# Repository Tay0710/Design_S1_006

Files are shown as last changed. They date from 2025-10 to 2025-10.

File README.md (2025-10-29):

# ELEC5550 Group Project (Team 0-06)

**Students Involved:**
- Aidan	Wheller
- Dorothy	Jong
- Emersyn Johnson
- Owen Spicer
- Samuel Dixon
- Taylah Karran

## 🚀 Project Summary

This project integrates hardware, firmware, and design elements to develop a fully functional autonomous 3D mapping drone system. This iteration of the design involves a drone capable of autonomously navigating the operation environment of Lv4 EECE, a LoRa-based kill switch which covers the entire operation environment, a mapping test rig used to manually collect data from 2 independent mapping systems, and a 3D mapping python pipeline which runs on the base station, used to convert raw mapping data from the test rig into 2 independent maps plus a combined map.

The next iteration of this design aims to combine the mapping test rig with the autonomous drone platform, creating a fully integrated autonomous 3D mapping drone system which follows the system architecture diagram below.

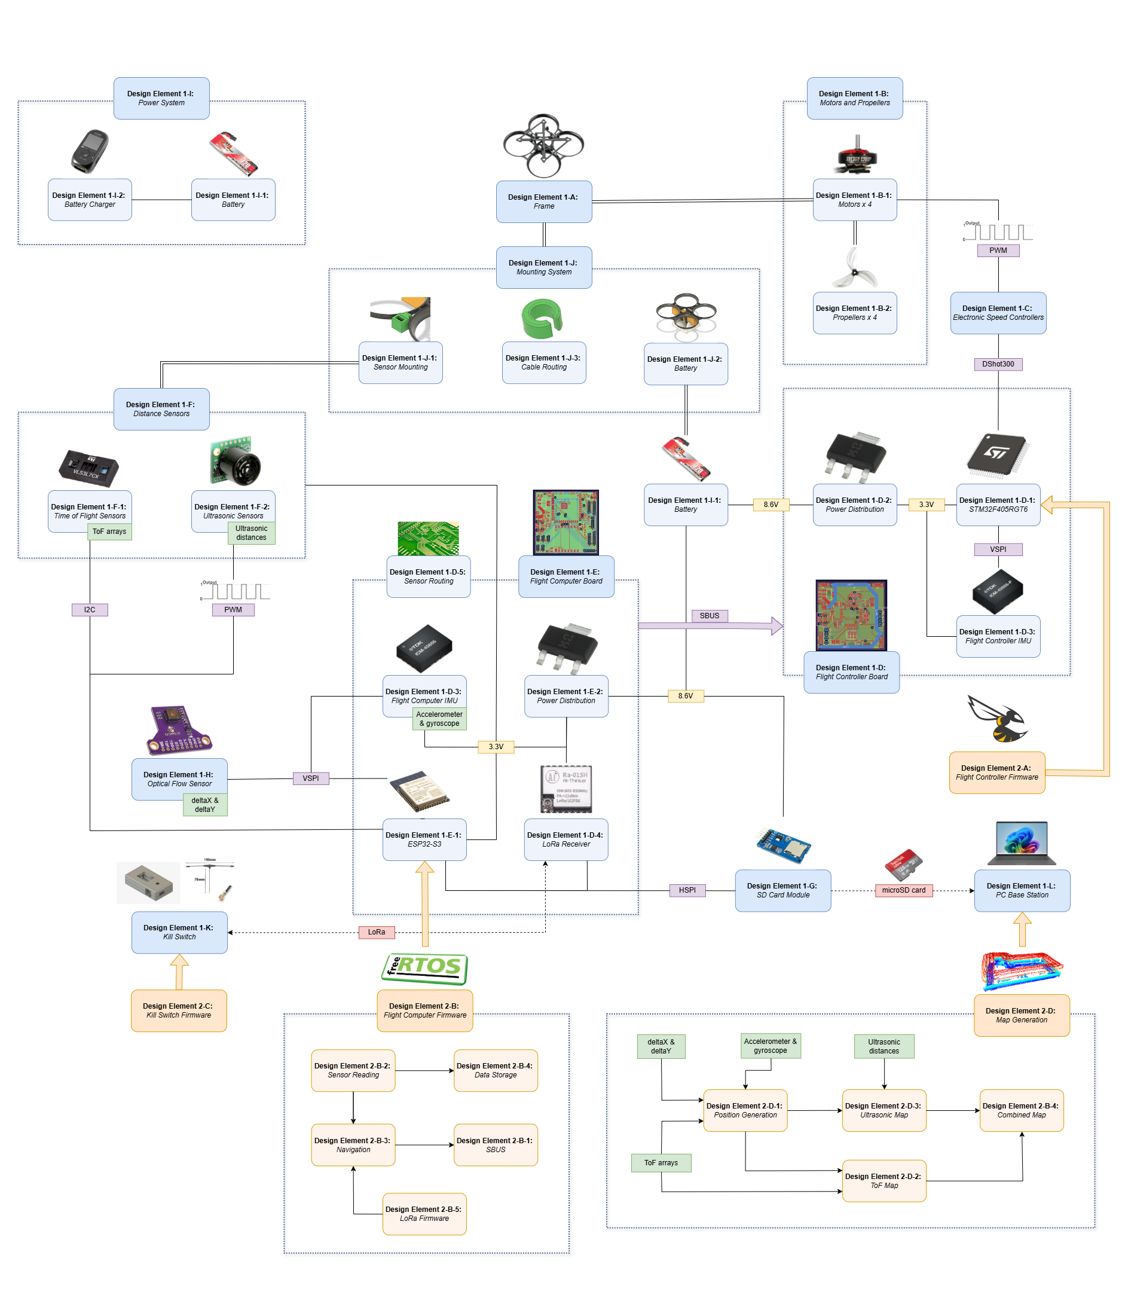
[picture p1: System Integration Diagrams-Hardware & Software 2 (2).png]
System Architecture


## 📁 Folder Structure

```
📁 Root Directory

├── 📂 3D Mapping
│   └── 3D mapping
│   └── optical_flow_method
│   └── optical_flow_method_data
│
├── 📂 CAD Design
│   └── 3D-printed Parts
│   └── Full_Model
│   └── LoRa Kill Switch
│
├── 📂 Drone Firmware
│   └── Flight Computer Firmware
│   └── Flight Controller Firmware
│
├── 📂 LoRa Drone Receiver Test Firmware
│   └── LORA_DRONE_RECEIVER
│
├── 📂 LoRa Kill Switch Firmware
│   └── LORA_TRANSMITTER_BUTTON
│
├── 📂 PCB Design
│   └── ESP32_BOARD_V2
│   └── STM32_BOARD_V3
│
├── 📂 Test Rig Firmware
│   └── Test Rig Data Collection
│   └── Test Rig FreeRTOS
│
└── 📂 Videos
```

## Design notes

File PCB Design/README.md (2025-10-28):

# ELEC5550 Group Project (Team 0-06)

**Students Involved:**
- Aidan	Wheller
- Dorothy Jong
- Emersyn Johnson
- Owen Spicer
- Samuel Dixon
- Taylah Karran

## 📁 Project Overview - PCB Design

**Folder Summary:**

This folder contains all PCB schematics, design files, and related documentation required for manufacturing the printed circuit board (PCB) for the ESP32 flight computer and STM32 flight controller. It includes the necessary Gerber files, bill of materials (BOM), and design source files to ensure accurate production and assembly. All PCB projects can be viewed through KiCAD, which can be downloaded through this [link](https://www.kicad.org/download/).

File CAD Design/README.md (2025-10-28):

# ELEC5550 Group Project (Team 0-06)

**Students Involved:**
- Aidan	Wheller
- Dorothy Jong
- Emersyn Johnson
- Owen Spicer
- Samuel Dixon
- Taylah Karran

## 📁 Project Overview - CAD Design

**Folder Summary:**

This folder contains all the CAD and STL files required to replicate the design. The CAD files can be used for editing in your preferred CAD software, and the STL files are ready for 3D printing. More specifically, it contains:
- LoRa Kill Switch: CAD and STL files for the LoRa Kill Switch Case.
- Full_Model: CAD project (on Fusion) for the drone assembly, including the drone frame, launch pad, launch rail and sensors mounts.
- 3D-printed Parts: STL files for the launch pad, launch rail, and various sensors mounts which were 3D-printed.

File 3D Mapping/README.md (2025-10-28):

# ELEC5550 Group Project

**Students Involved:**
- Aidan	Wheller
- Dorothy Jong
- Emersyn Johnson
- Owen Spicer
- Samuel Dixon
- Taylah Karran

## 📁 Project Overview
This repository contains all scripts used to process sensor data and generate a **3D map** of an indoor environment using a drone platform equipped with:
- PMW3901 Optical Flow Sensor  
- VL53L7CX Time-of-Flight (ToF) Sensor  
- Ultrasonic Distance Sensors (U, D, L, R)  
- ICM-45686 IMU  

The system estimates **drone position and orientation** in the world frame and then maps the environment using synchronized ToF and Ultrasonic readings.

---

## Execution Order

### **A. Install the Virtual Environment**
1. From the project root folder, run:
        python -m venv venv
2. Run the virtual environment:
        .\venv\Scripts\activate
3. Install all required packages:
        pip install -r requirements.txt
Note: to get open3d working must use python 11 or below.

### **B. Position and Trajectory Estimation**
1. Open the optical flow position folder:
        cd optical_flow_method
2. Update the filepath in x0_position_pipeline.py
3. Run the position pipeline:
        python x0_position_pipeline.py

### **C. Point Cloud Generation**
1. Exit the optical flow folder:
        cd ..
2. Open the 3D mapping folder:
        cd 3D mapping
3. Update the filepath in x0_mapping_pipeline_V3.py
4. Run the mapping pipeline:
        python x0_mapping_pipeline_V3.py
##

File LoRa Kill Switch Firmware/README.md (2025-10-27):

# ELEC5550 Group Project (Team 0-06)

**Students Involved:**
- Aidan	Wheller
- Dorothy Jong
- Emersyn Johnson
- Owen Spicer
- Samuel Dixon
- Taylah Karran

## 📁 Project Overview - LoRa Kill Switch Firmware

This folder contains the firmware for the LoRa Kill Switch. It is intended for a LilyGo T3 S3 SX1262 board with an IPEX-connected 915 MHz T-antenna. This firmware is responsible for sending LoRa messages periodically to the LoRa receiver on the flight computer PCB. 

---
## Execution Order
### **A. Install VSCode and PlatformIO**
1. To run PlatformIO, download VSCode from the following [link](https://platformio.org/platformio-ide).
1. Open Extensions in VSCode and download PlatformIO from VSCode Extensions.

### **B. Uploading the Firmware**
1. Open the LORA_TRANSMITTER_BUTTON folder as a project in PlatformIO.
1. Connect the LilyGo T3 S3 SX1262 board to your PC via the USB-C port. Note: Ensure that the LilyGo T3 SX1262 board power switch is turned on.
1. Click the upload button on the PlatformIO to upload the firmware. Note: you may need to enter boot mode. To do this, open the case and press the boot button when resetting or powering on the board.

### **C. Using the LoRa Kill Switch**
1. To use the LoRa Kill Switch, power it using a USB-C cable.
1. Make sure that the T-antenna is connected properly.
1. Turn on the kill switch via the power switch at the bottom.
1. To start autonomous operation on the drone, press the red button once (as stated on the OLED display).
1. To stop the drone, press the red button a second time.

Note: make sure that the kill switch is not transmitting any LoRa messages when the drone is first powered on.

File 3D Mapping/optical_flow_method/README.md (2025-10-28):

This is the code for the 3D drone trajectory.
To update this for new samples:
    - Run x0_position_pipeline.py to update all position data.

To run:
    - Run x0_mapping_pipeline.py to generate the drone trajectory in world frame.

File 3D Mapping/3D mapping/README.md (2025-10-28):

This is the code for the 3D mapping using the position calculated in the pipeline.
To update this for new samples:
    - Run x0_mapping_pipeline_V3.py to update all position data.

To run:
    - Run x0_mapping_pipeline_V3.py to generate point clouds of the:
        1. ToFs
        2. Ultrasonics
        3. Fused Map

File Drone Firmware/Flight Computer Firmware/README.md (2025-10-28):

# ELEC5550 Group Project (Team 0-06)

**Students Involved:**
- Aidan	Wheller
- Dorothy Jong
- Emersyn Johnson
- Owen Spicer
- Samuel Dixon
- Taylah Karran

## 📁 Project Overview - Flight Computer Firmware

This folder contains the flight computer firmware intended for the custom flight computer PCB. The purpose of this firmware is to autonomously fly the drone by sending flight commands, through SBUS protocol, which are generated by the onboard flight control algorithms. The autonomous flight control algorithm is largely based on a left-wall following algorithm, with ultrasonic and ToF array sensors used to detect the walls and other obstacles. The drone maintains a constant distance from the wall by adjusting its roll (sent via SBUS) using a modified PD-control loop.

---
## Execution Order
### **A. Install VSCode and PlatformIO**
1. To run PlatformIO, download VSCode from the following [link](https://platformio.org/platformio-ide).
1. Open Extensions in VSCode and download PlatformIO from VSCode Extensions.

### **B. Uploading the Firmware** 
1. Open the Flight_Computer_Autonomous_Flight folder as a project in PlatformIO.
1. Connect the ESP32-S3 flight computer board to your PC via the USB micro-B port.
1. Click the upload button on the PlatformIO to upload the firmware. Note: you may need to enter boot mode. To do this, press the boot button when resetting or powering on the board.

### **C. Executing a Scan**
1. Remove USB connection to laptop/PC.
2. Make sure that the LoRa kill switch is switched off.
3. As instructed in the user manual, make sure to position the drone using the launch rails and launch pad. Plug in the 2S battery. Wait 5 seconds for the IMU to calibrate.
4. Remove the launch rails and place the drone on the launch pad at the starting position.
5. Power on the LoRa kill switch.
6. To begin autonomous operation, press the red button on the LoRa kill switch. The OLED display on the kill switch displays the message being transmitted.
7. To stop autonomous opeartion, press the red button on the LoRa kill switch again to send a "STOP" message, killing power to all the motors within 5 seconds.

Note: the red LED on the flight controller PCB indicates that the PCB is being powered.

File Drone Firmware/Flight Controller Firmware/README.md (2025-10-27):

# ELEC5550 Group Project (Team 0-06)

**Students Involved:**
- Aidan	Wheller
- Dorothy Jong
- Emersyn Johnson
- Owen Spicer
- Samuel Dixon
- Taylah Karran

## 📁 Project Overview - Flight Controller Firmware (BetaFlight)

This folder contains the flight controller firmware intended for the STM32F405RGT6 microcontroller on the flight controller PCB. The purpose of this firmware is to manage and stabilise the vehicle’s flight dynamics, processing IMU data and control inputs to generate precise motor and actuator commands.
The firmware is based on the open-source project *BetaFlight*, with a custom configuration tailored specifically for this system. 

---
## Execution Order
### **A. Install STM32CubeProgrammer**
1. Download the STM32CubeProgrammer from this [link](https://www.st.com/en/development-tools/stm32cubeprog.html).
1. Make sure to download the correct version for your PC.

### **B. Flashing the Firmware**
1. Download FLIGHT_CONTROLLER_V1.hex.
1. Open the *STM32CubeProgrammer*.
1. Using an ST-Link, connect SWDIO, SWDCLK, VDD and GND on the flight controller PCB to a PC running STM32CubeProgrammer.
1. Select 'ST-LINK' as the flashing method.
1. Go to the 'Erase & Programming' tab and select the file path of the FLIGHT_CONTROLLER_V1.hex file.
1. Click 'Start Programming' to flash the firmware onto the flight controller PCB.

Note: the LED on the flight controller PCB will start to flash, indicating that the firmware has been uploaded correctly.

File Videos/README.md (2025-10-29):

# ELEC5550 Group Project (Team 0-06)

**Students Involved:**
- Aidan	Wheller
- Dorothy Jong
- Emersyn Johnson
- Owen Spicer
- Samuel Dixon
- Taylah Karran

## 📁 Project Overview - Videos

This folder contains videos of the drone system in operation.

---
## Video Descriptions

### **Drone_Autonomous_Flight_Compressed.mp4**
This video was filmed after hours. It shows the drone successfully navigating autonomously down the length of the hallway, then turning right upon reaching a wall, and then navigating down the second hallway. No bystanders or uninvolved personnel were present during filming for safety reasons.

### **Custom_PCB_Motor_Test_Video.mp4**
This video shows each motor in operation while connected to our custom flight controller PCB and commercial ESCs.

### **Left_Turn_Video.mp4**
This video shows the drone autonomously turning left when there is a corner. This was filmed in the designated testing zone of the Lycopodium Laboratory.

### **Video_From_Demonstration**
This is the video from the official demonstration.

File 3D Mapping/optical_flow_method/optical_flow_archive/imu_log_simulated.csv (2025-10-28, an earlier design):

millis | ax | ay | az | gx | gy | gz
0 | 0.0 | 0.0 | 0.0 | 0.0 | 0.0 | 0.0
10 | 0.003970010072162657 | -0.004143366628477348 | 1.009922869792396 | 0.04246248867841663 | -0.023719845371533477 | 0.03823164368084453
20 | -0.005630144648727487 | 0.006787736788023693 | 1.003133558558664 | 0.06204213521290253 | -0.03606169442252252 | 0.044796276796084264
30 | -0.005310671083645506 | -0.01964439691232883 | 1.0145801393593221 | 0.05388330169073391 | -0.021868536522935647 | 0.0386054729523965
40 | 0.006911457807997143 | 0.0003999330672221197 | 1.0043240633648682 | 0.06436539555835025 | -0.033661465325746945 | 0.03786024592444924
50 | -0.00151988489667531 | -0.01373503787305486 | 1.0119983379776263 | 0.046078438197613245 | -0.03780757874279826 | 0.05168775226637012
60 | -0.01626483354697924 | -0.0038154610411281604 | 0.996990700934959 | 0.032843364613086734 | -0.04456380213117112 | 0.03727785231403848
70 | -0.0021146940481681434 | -0.020732915467909733 | 1.001214343840099 | 0.04124647142253926 | -0.034114377811272516 | 0.04151161903881539
80 | 0.002938775146978739 | 0.006540030118819065 | 1.0155701558688028 | 0.04394749827191787 | -0.009172993606722406 | 0.05659510750858936
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

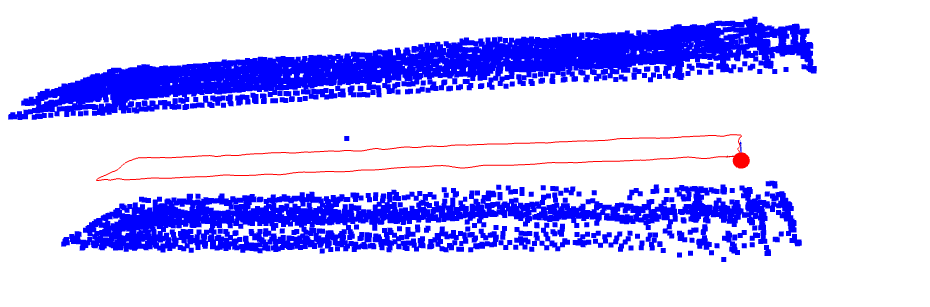
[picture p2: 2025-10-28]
3D Mapping/3D mapping/Images/22_09_25_1_rectangle_up_down.png

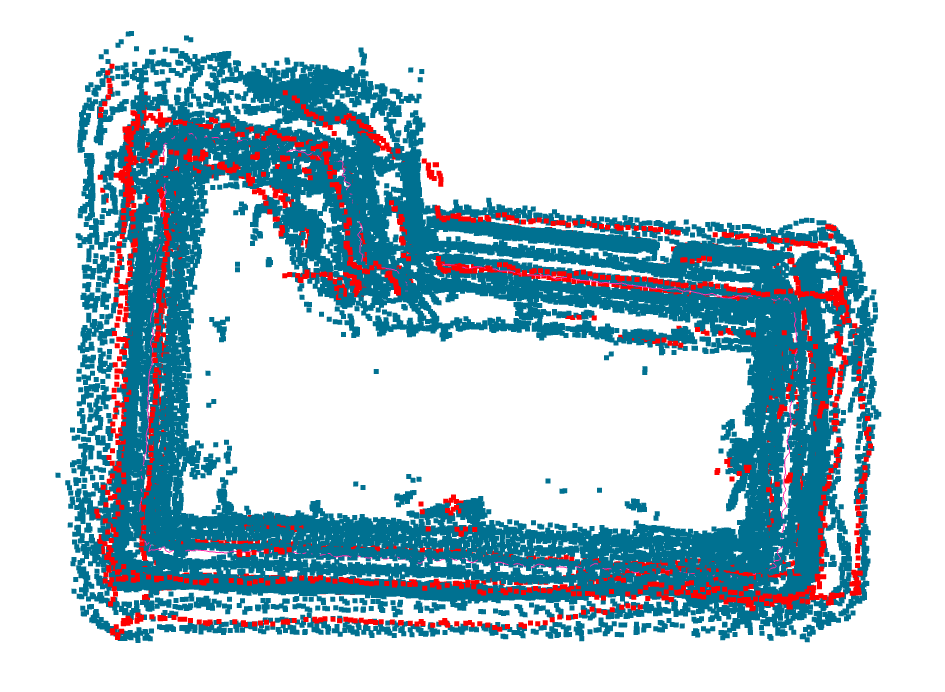
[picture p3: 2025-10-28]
3D Mapping/3D mapping/Images/Distance Constrained.png

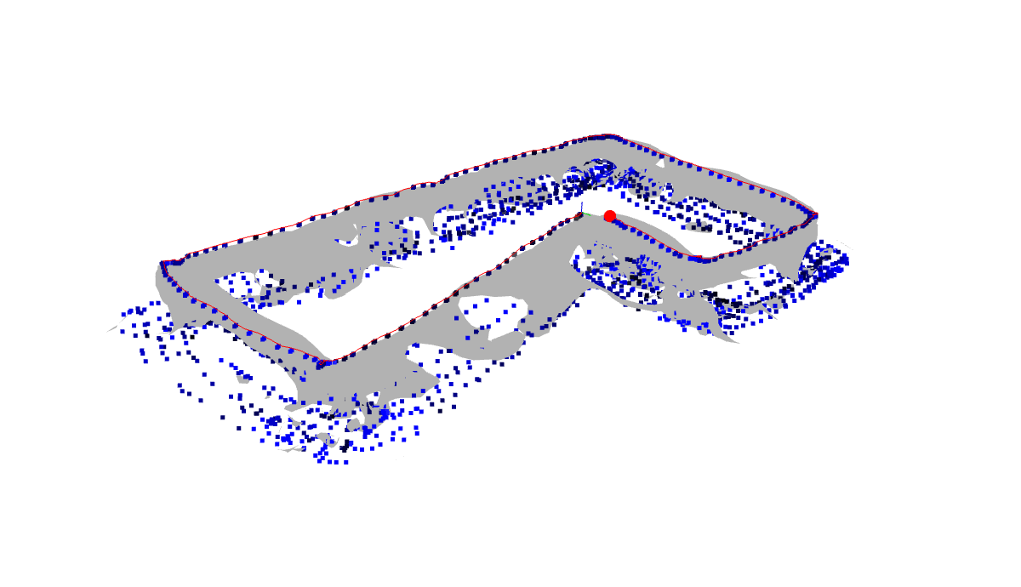
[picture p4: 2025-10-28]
3D Mapping/3D mapping/Images/Single ToF, Mesh with Outliers.png

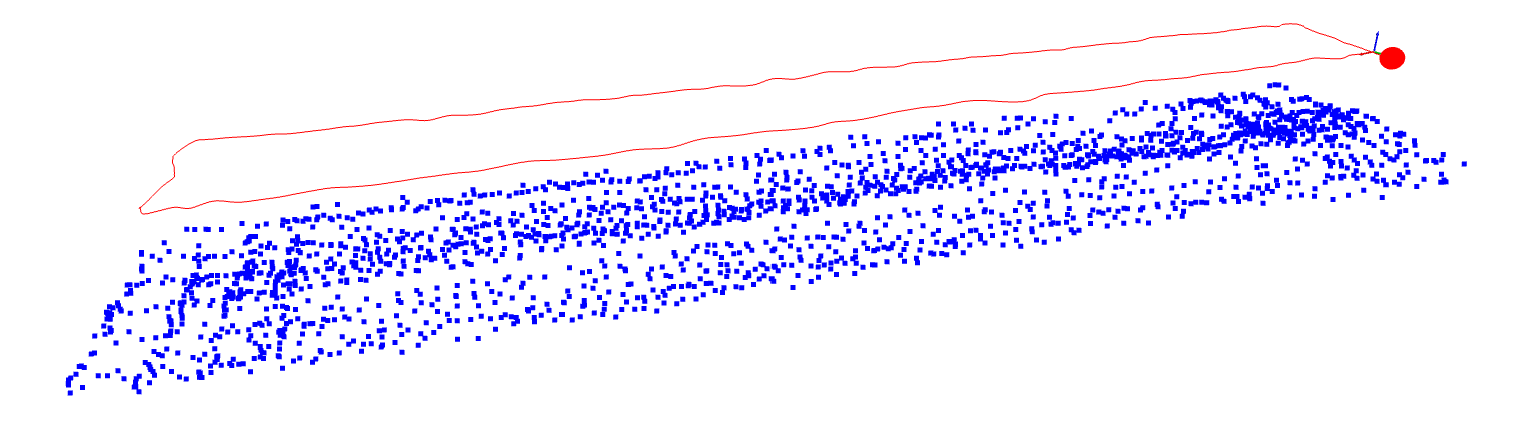
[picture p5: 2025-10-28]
3D Mapping/3D mapping/Images/22_09_25_1_rectangle_down.png

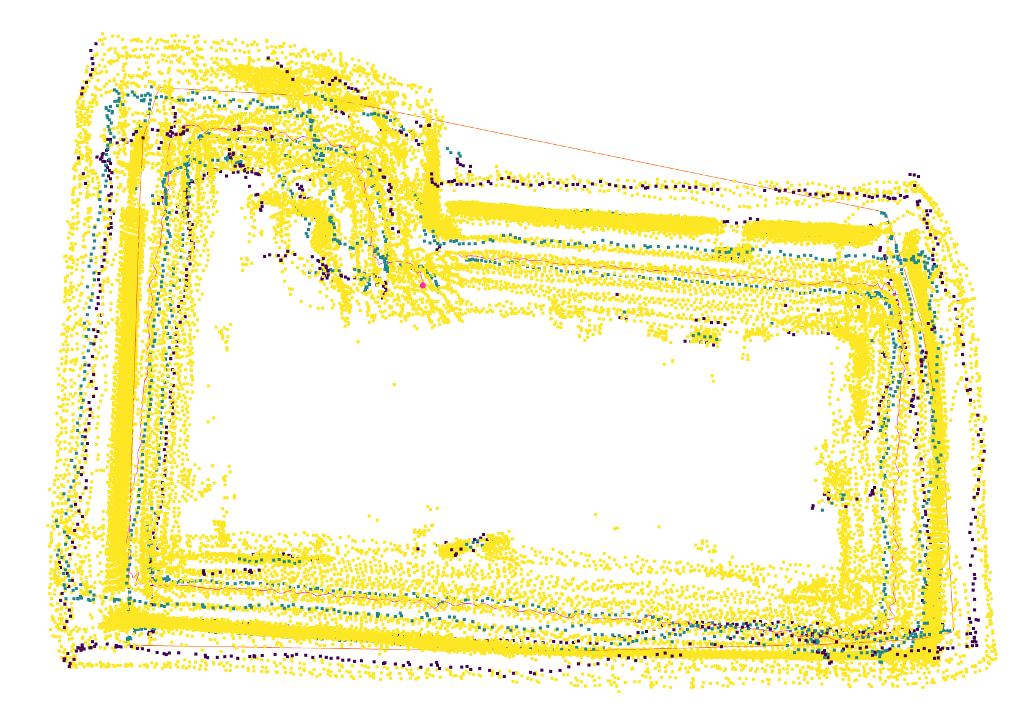
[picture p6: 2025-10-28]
3D Mapping/3D mapping/Images/Fully Filtered.png

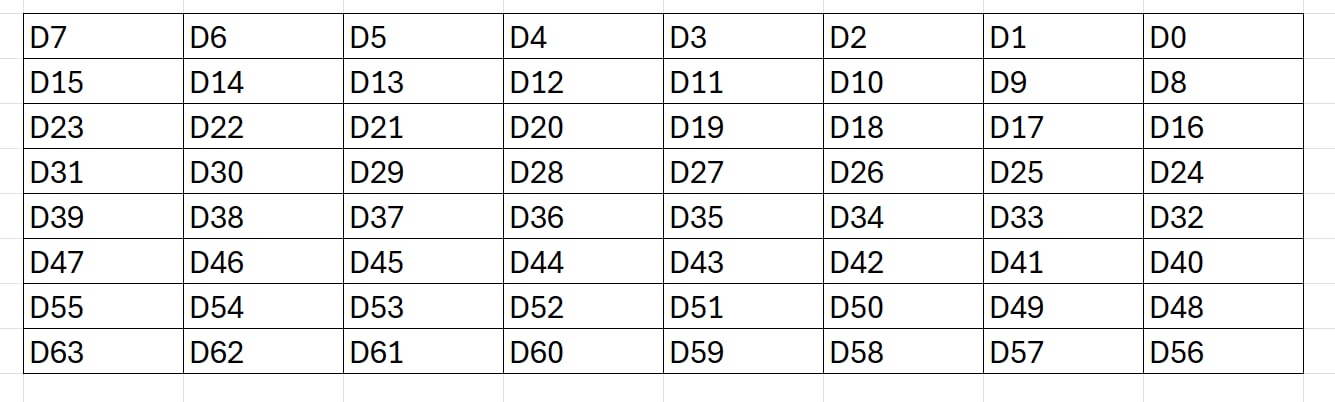
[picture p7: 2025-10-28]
3D Mapping/3D mapping/ToF_8x8.jpeg

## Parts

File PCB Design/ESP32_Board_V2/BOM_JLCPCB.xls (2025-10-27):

Comment | Designator | Footprint | JLCPCB Part#(optional)
100nF/16V | C9, C12, C13, C14, C23 | 402 | C1525
10uF/25V | C11, C15, C17, C19, C20 | 805 | C15850
BAT54C | D6 | SOT-23 | C2135
KT-0603R | D4 | 0603_LED | C2286
KT-0603W | D5 | 0603_LED | C2290
Connector_USB:USB_Micro-B_Amphenol_10103594-0001LF_Horizontal | J6 | SMD | C428495
10k/100mW | R12 | 0603_R | C25804
22/100mW | R10, R11 | 0603_R | C23345
1k/100mW | R8, R9 | 0603_R | C21190
TS-1187A-B-A-B | S1, S2 | SMD | C318884
NCP1117ST50T3G | U3 | SOT-223 | C17314
NCP1117ST33T3G | ESP3V3 | SOT-223 | C26537
D3V3XA4B10LP | U5 | UDFN2510-10 | C1980462
ICM-45686 | U7 | LGA-14(3x2.5) | C22459454
ESP32-S3-WROOM-1U | U1 | SMD,18x19.2mm | C2980298

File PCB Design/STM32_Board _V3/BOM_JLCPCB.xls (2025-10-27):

Comment | Designator | Footprint | JLCPCB Part#(optional)
100nF/16V | C1, C2, C3, C4, C5, C6, C7, C10, C20, | 402 | C1525
10uF/25V | C8, C9 | 805 | C15850
2.2nF/50V | C21 | 603 | C1604
10nF/50V | C22 | 805 | C1710
BAT45C | D1 | SOT-23 | C2135
KT-0603R | D2 | 0603_LED | C2286
KT-0603W | D3 | 0603_LED | C2290
USB_Micro-AB_Molex_47590-0001 | J1 | USB_Micro-AB_Molex_47590-0001 | C136001
10k/100mW | R1, R4, R5 | 0603_R | C25804
22/100mW | R2, R3 | 0603_R | C23345
1k/100mW | R6, R7 | 0603_R | C21190
TS-1187A-B-A-B | S2 | SMD | C318884
NCP1117ST33T3G | STM3V3 | SOT-223 | C26537
STM32F405RGT6 | U2 | LQFP-64(10x10) | C15742
ICM-42688-P | U4 | LGA-14(2.5x3) | C1850418
SN74LVC1G04DBVR | U6 | SOT-23-5 | C7827
XTAL_ABM8AIG-8.000MHZ-1Z-T | Y2 | XTAL_ABM8AIG-8.000MHZ-1Z-T | C5140594

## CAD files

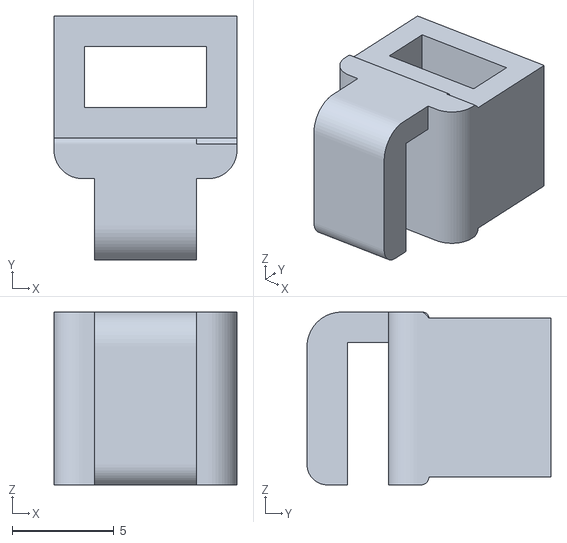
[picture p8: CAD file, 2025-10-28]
CAD Design/3D-printed Parts/SENSOR_MOUNT_3.stl
9.00 x 12.0 x 8.50

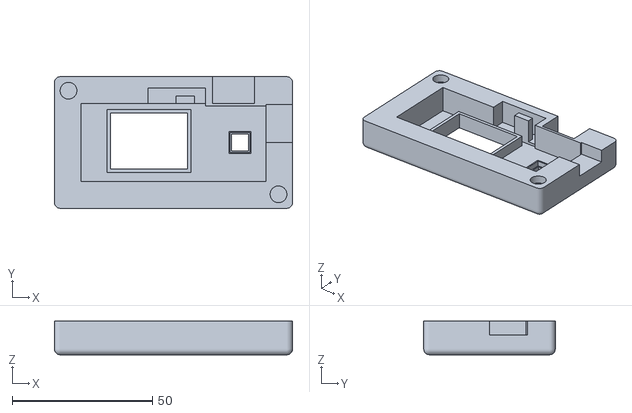
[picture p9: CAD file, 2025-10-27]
CAD Design/LoRa Kill Switch/STL Files/TOP v14.stl
85.0 x 47.0 x 12.0

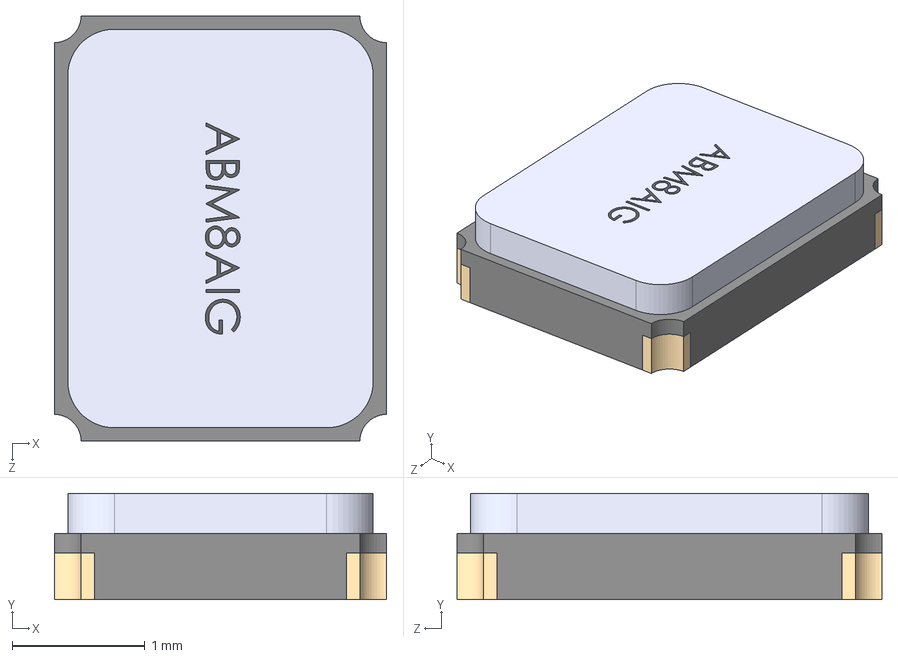
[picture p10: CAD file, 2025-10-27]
PCB Design/ESP32_Board_V2/ABM8AIG_8_000MHZ_1Z_T/ABM8AIG-8.000MHZ-1Z-T.step
2.50 x 0.801 x 3.20 mm

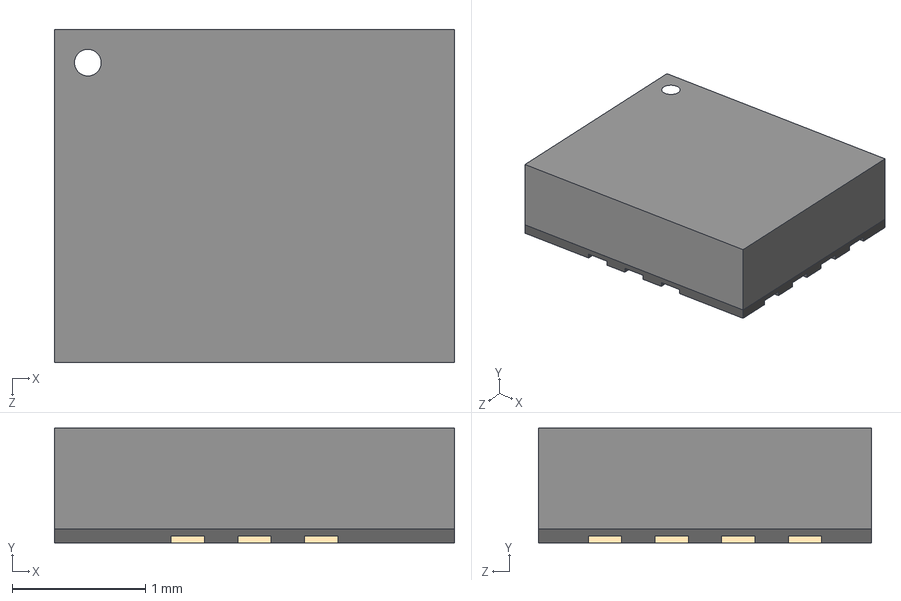
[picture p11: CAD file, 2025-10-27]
PCB Design/ESP32_Board_V2/ICM_45686/ICM-45686.step
3.00 x 0.86 x 2.50 mm

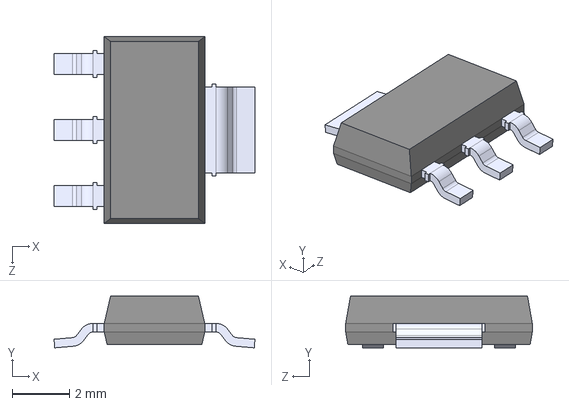
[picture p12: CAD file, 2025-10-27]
PCB Design/ESP32_Board_V2/NCP1117ST33T3G.step
7.00 x 1.80 x 6.50 mm

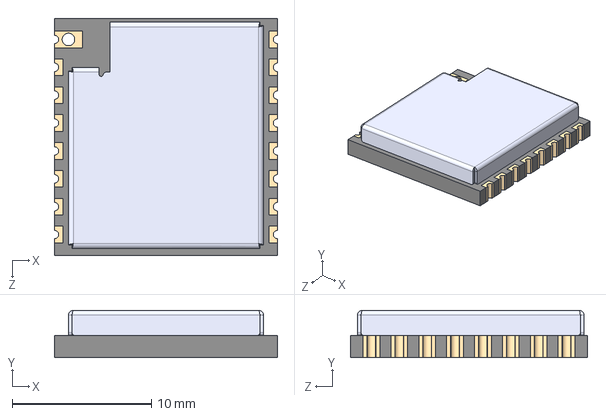
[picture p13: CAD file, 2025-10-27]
PCB Design/ESP32_Board_V2/RA-01H/RA-01H.step
16.0 x 3.40 x 17.0 mm

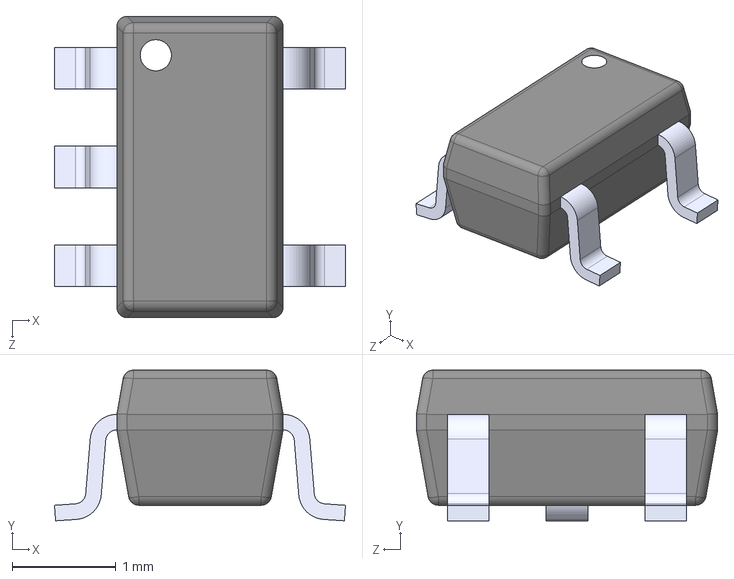
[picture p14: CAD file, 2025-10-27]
PCB Design/ESP32_Board_V2/SN74LVC1G04DBVR/SN74LVC1G04DBVR.step
2.80 x 1.45 x 2.90 mm

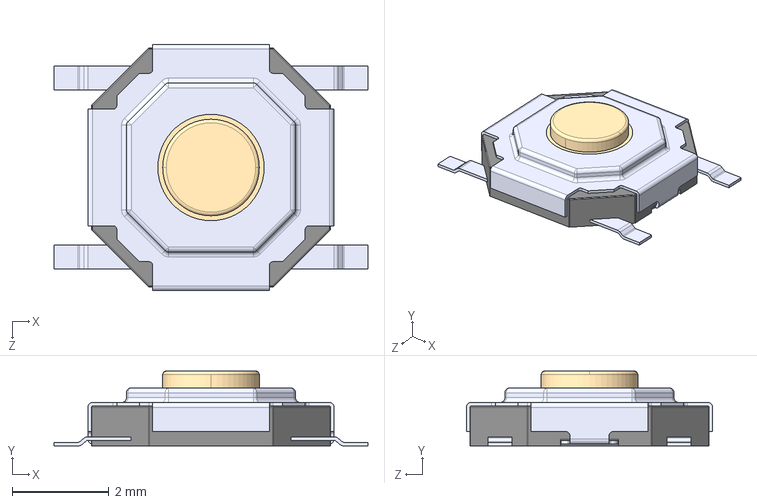
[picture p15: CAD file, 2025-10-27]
PCB Design/STM32_Board _V3/TS-1187A-B-A-B/TS-1187A-B-A-B.step
6.50 x 1.55 x 5.10 mm

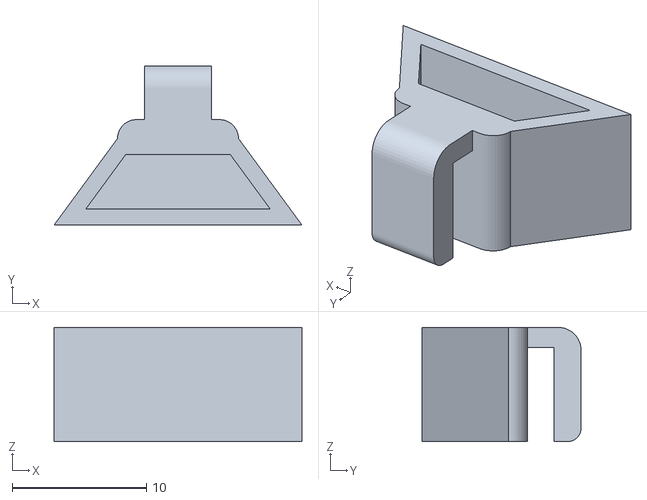
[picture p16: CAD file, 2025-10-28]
CAD Design/3D-printed Parts/SENSOR_MOUNT_1.stl
18.5 x 11.9 x 8.50

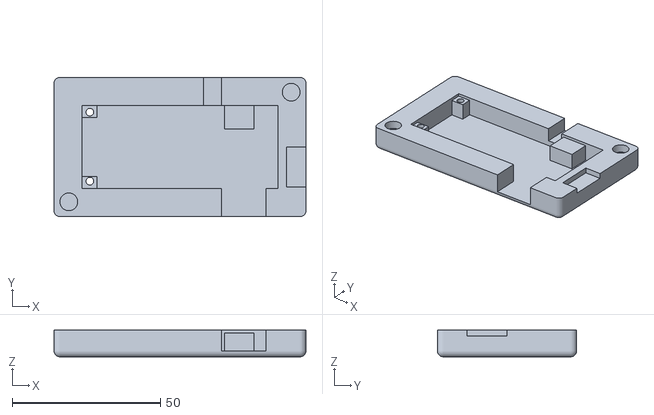
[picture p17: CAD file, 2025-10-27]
CAD Design/LoRa Kill Switch/STL Files/BOTTOM v13.stl
85.0 x 47.0 x 9.00

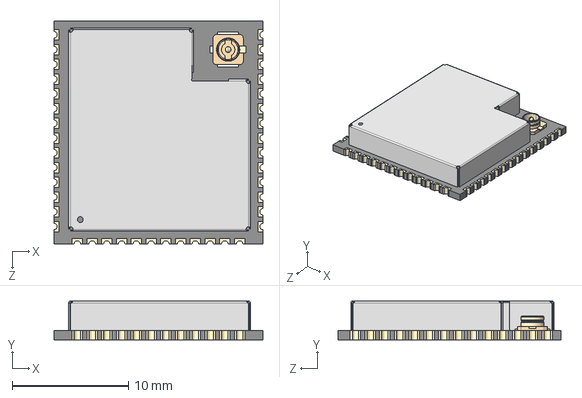
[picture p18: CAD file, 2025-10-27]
PCB Design/ESP32_Board_V2/ESP32-S3-WROOM-1U.step
18.0 x 3.35 x 19.2 mm

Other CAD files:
3D Mapping/3D mapping/Mapping archive/parallel_mesh.ply
3D Mapping/3D mapping/Mapping archive/parallel_pointcloud.ply
CAD Design/3D-printed Parts/LAUNCHPAD.stl
CAD Design/3D-printed Parts/LAUNCHRAIL.stl
CAD Design/3D-printed Parts/SENSOR_MOUNT_2.stl
CAD Design/3D-printed Parts/SENSOR_MOUNT_4.stl
CAD Design/Full_Model/Drone_3D_Model.f3d
CAD Design/LoRa Kill Switch/ASSEMBLY v9.f3z
CAD Design/LoRa Kill Switch/CAD Files/BOTTOM v13.f3d
CAD Design/LoRa Kill Switch/CAD Files/TOP v14.f3d

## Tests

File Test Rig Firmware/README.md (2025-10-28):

# ELEC5550 Group Project

**Students Involved:**
- Aidan	Wheller
- Dorothy Jong
- Emersyn Johnson
- Owen Spicer
- Samuel Dixon
- Taylah Karran

## 📁 Project Overview - Test Rig Firmware

This folder contains the firmware for the mapping test rig used to simulate mapping on-board the drone and firmware prepared to integrate the mapping and autonomous flight systems. Samples were collected using a custom-made ESP32-S3 flight computer PCB and the sensors listed below:
- PMW3901 optical flow camera
- 4 * VL53L7CX time of flight sensors
- 3 * MB1030 ultrasonic sensors
- ICM-45686 inertial measurement unit
- Generic SD card module

---
## Execution Order - Test Rig Data Collection
### **A. Install VSCode and PlatformIO**
1. To run PlatformIO, download VSCode from the following [link](https://platformio.org/platformio-ide).
1. Open Extensions in VSCode and download PlatformIO from VSCode Extensions.

### **B. Uploading the Firmware** 
1. Open the Test Rig Data Collection folder as a project in PlatformIO.
1. Connect the ESP32-S3 flight computer board to your PC via the USB micro-B port.
1. Click the upload button on the PlatformIO to upload the firmware. Note: you may need to enter boot mode. To do this, open the test rig and press the boot button when resetting or powering on the board.

### **C. Executing a Scan**
1. Remove USB connection to laptop/PC and plug in the 2S battery. The power PCB LED should activate.
1. Secure the test rig such that the PCB is flat and press the calibration button. The white PCB LED should activate.
1. Hold the test rig still until the white PCB LED switches off, indicating setup is complete.
1. Position the test rig at the start of the sample location and press the calibration button to begin sampling (mode = TRUE).
1. Walk the intended scan route.
1. Press the calibration button to end the sample (mode = FALSE).
1. Wait 5 seconds then remove the battery and microSD card.
1. Transfer scan files to the data folder of the Design_S1_006 GitHub repository.

### **Output Files**
CSV output files:

    imu_ICM45686.csv
        returns: time, gyro x, gyro y, gyro z, accel x, accel y, accel z
        units: s, dps, dps, dps, g, g, g

    tof_L7.csv
        returns: time, type, D0, ..., D63
        units: s, [refer below], mm, ..., mm
        type: L, R, U, D (refers to the specific ToF being called upon)

    of_PMW3901.csv
        returns: time, deltaX, deltaY, SQUAL, SHUTTER
        units: s, [unitless], ..., [unitless]

    Ultra_MB1030.csv
        returns: time, type, distance
        units: s, [refer below], cm
        type: L, R, U (refers to the specific ultrasonic sensor being called upon)

---
## Test Rig FreeRTOS

Firmware was prepared to integrate the mapping and autonomous flight systems using FreeRTOS. The Test Rig FreeRTOS folder contains a PlatformIO project that can sample mapping sensors on-board the drone with minimal impact on the navigation algorithm.

### **Priority Logic**

| Task Name | Purpose | Rate/Freq | Priority | Core |
| --- | --- | --- | --- | --- |
| `ultrasonic_ctrl` | Flight control via SBUS | 20 Hz | 🔴 High | Core 1 |
| `tof_mapping` | Primary mapping (ToF) | 15 or 60Hz  | 🟠 Med | Core 0 |
| `ultrasonic_map`  | Secondary mapping (Ultrasonics) | 20 Hz | 🟠 Med | Core 0 |
| `imu_logger` | IMU raw logging | 100 Hz | 🟡 Med-Low | Core 0 |
| `optflow_logger`  | Optical Flow raw logging | 50 - 100 Hz | 🟡 Med-Low | Core 0 |
| `lora_heartbeat`  | Alive signal check | 1 Hz | 🟢 Low | Core 0 |
| `logging_mgr` | Batch CSV writes to SD | 5–10 Hz | 🟢 Low | Core 0 |

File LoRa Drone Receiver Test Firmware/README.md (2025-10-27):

# ELEC5550 Group Project (Team 0-06)

**Students Involved:**
- Aidan	Wheller
- Dorothy Jong
- Emersyn Johnson
- Owen Spicer
- Samuel Dixon
- Taylah Karran

## 📁 Project Overview - LoRa Drone Receiver Test Firmware

This folder contains the firmware to test the range of the LoRa receiver on board the drone. It simply prints the payload and corresponding RSSI, SNR, and time between each LoRa message for each message received. 

---
## Execution Order
### **A. Install VSCode and PlatformIO**
1. To run PlatformIO, download VSCode from the following [link](https://platformio.org/platformio-ide).
1. Open Extensions in VSCode and download PlatformIO from VSCode Extensions.

### **B. Uploading the Firmware**
1. Open the LORA_DRONE_RECEIVER folder as a project in PlatformIO.
1. Connect the flight computer PCB to your PC via the micro-USB port.
1. Click the upload button on the PlatformIO to upload the firmware. Note: you may need to enter boot mode. To do this, open the case and press the boot button when resetting or powering on the board.

### **C. Testing the range of the LoRa receiver**
1. Power the LoRa Kill Switch and press the start button to begin LoRa transmission. Keep the LoRa kill switch at the base station.
1. Connect the flight computer to a Serial Monitor using a micro-USB cable. Make sure that the motors are NOT powered using a LiPo battery.
1. Walk around the designated operation zone with the drone and view the messages as well as the RSSI, SNR, and time between messages on the Serial Monitor connected to the flight computer to ensure that the LoRa antenna has sufficient range within the operation zone.

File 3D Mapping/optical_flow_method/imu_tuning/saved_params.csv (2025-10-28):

timestamp | gain | gyro_range | accel_rej | mag_rej | rej_timeout_mult | motion_threshold | smoothing_margin_mult | err_xy
2025-09-05 16:20:53 | 0.5 | 250 | 5 | 0 | 8 | 0.15 | 3 | 0.0005560094400059876

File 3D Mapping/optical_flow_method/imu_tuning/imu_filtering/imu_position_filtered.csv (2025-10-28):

time | vx | vy | vz | px | py | pz
7.28541 | -0.9552388478384878 | 0.847992853962104 | -0.1807383325154297 | 0.0 | 0.0 | 0.0
7.28604 | -0.9551126381725823 | 0.8478244694967314 | -0.18070049910593894 | -0.0006017209620488514 | 0.0005341294157830514 | -0.0001138413144367651
7.286666 | -0.954980206564053 | 0.8476458406355022 | -0.1806612534255961 | -0.0011995385713583875 | 0.0010647557120212652 | -0.0002269352590812713
7.287293 | -0.9548461565883691 | 0.8474635486082821 | -0.1806133390196684 | -0.001798227111539019 | 0.0015961153569984134 | -0.0003401798226465512
7.287918 | -0.9547137046663909 | 0.8472875123740538 | -0.18055335545466178 | -0.0023949231769558187 | 0.002125670052232468 | -0.00045302566980577255
7.288544 | -0.9545843390726422 | 0.8471203623872414 | -0.18047871285211947 | -0.0029924929732148835 | 0.002655967399086518 | -0.000566005344051122
7.289169 | -0.9544660138326195 | 0.846962689442548 | -0.18038617240312205 | -0.003589034231860576 | 0.0031853190799883816 | -0.0006787467018031309
7.289794 | -0.9543588483371763 | 0.8468113461376696 | -0.1802728850073242 | -0.004185508512070769 | 0.0037145761713239436 | -0.000791417254932606
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

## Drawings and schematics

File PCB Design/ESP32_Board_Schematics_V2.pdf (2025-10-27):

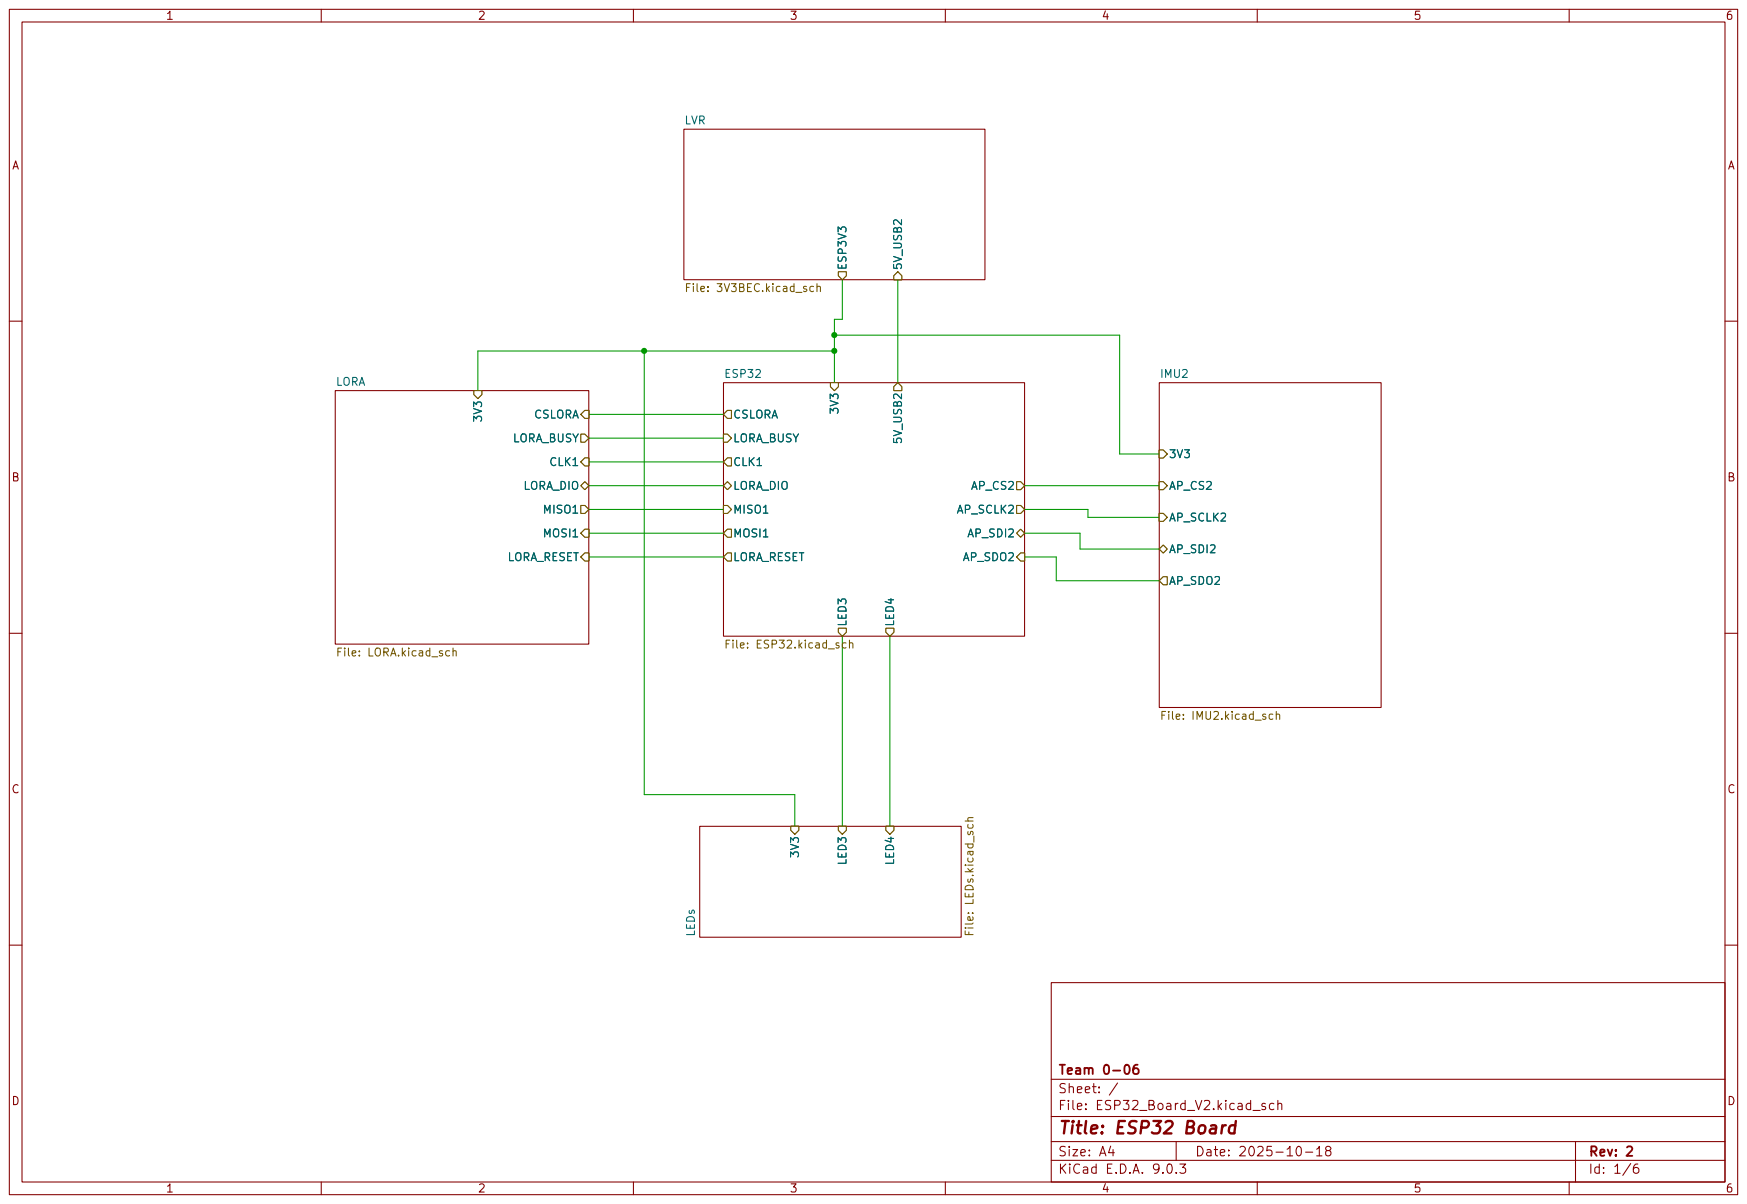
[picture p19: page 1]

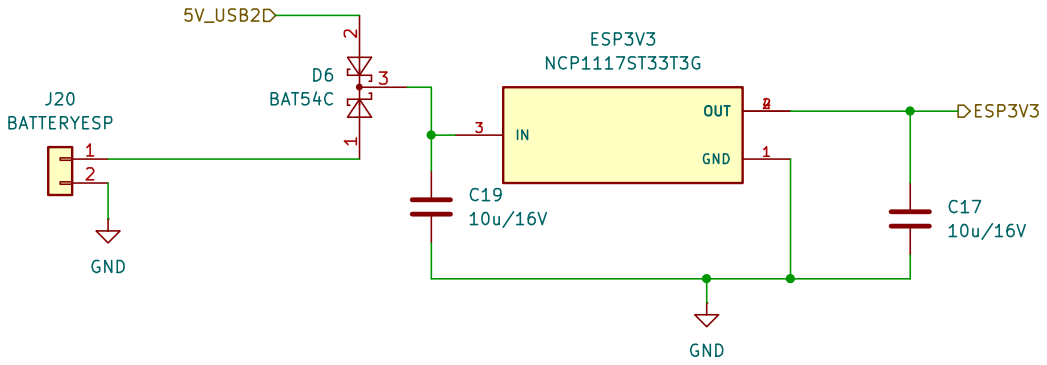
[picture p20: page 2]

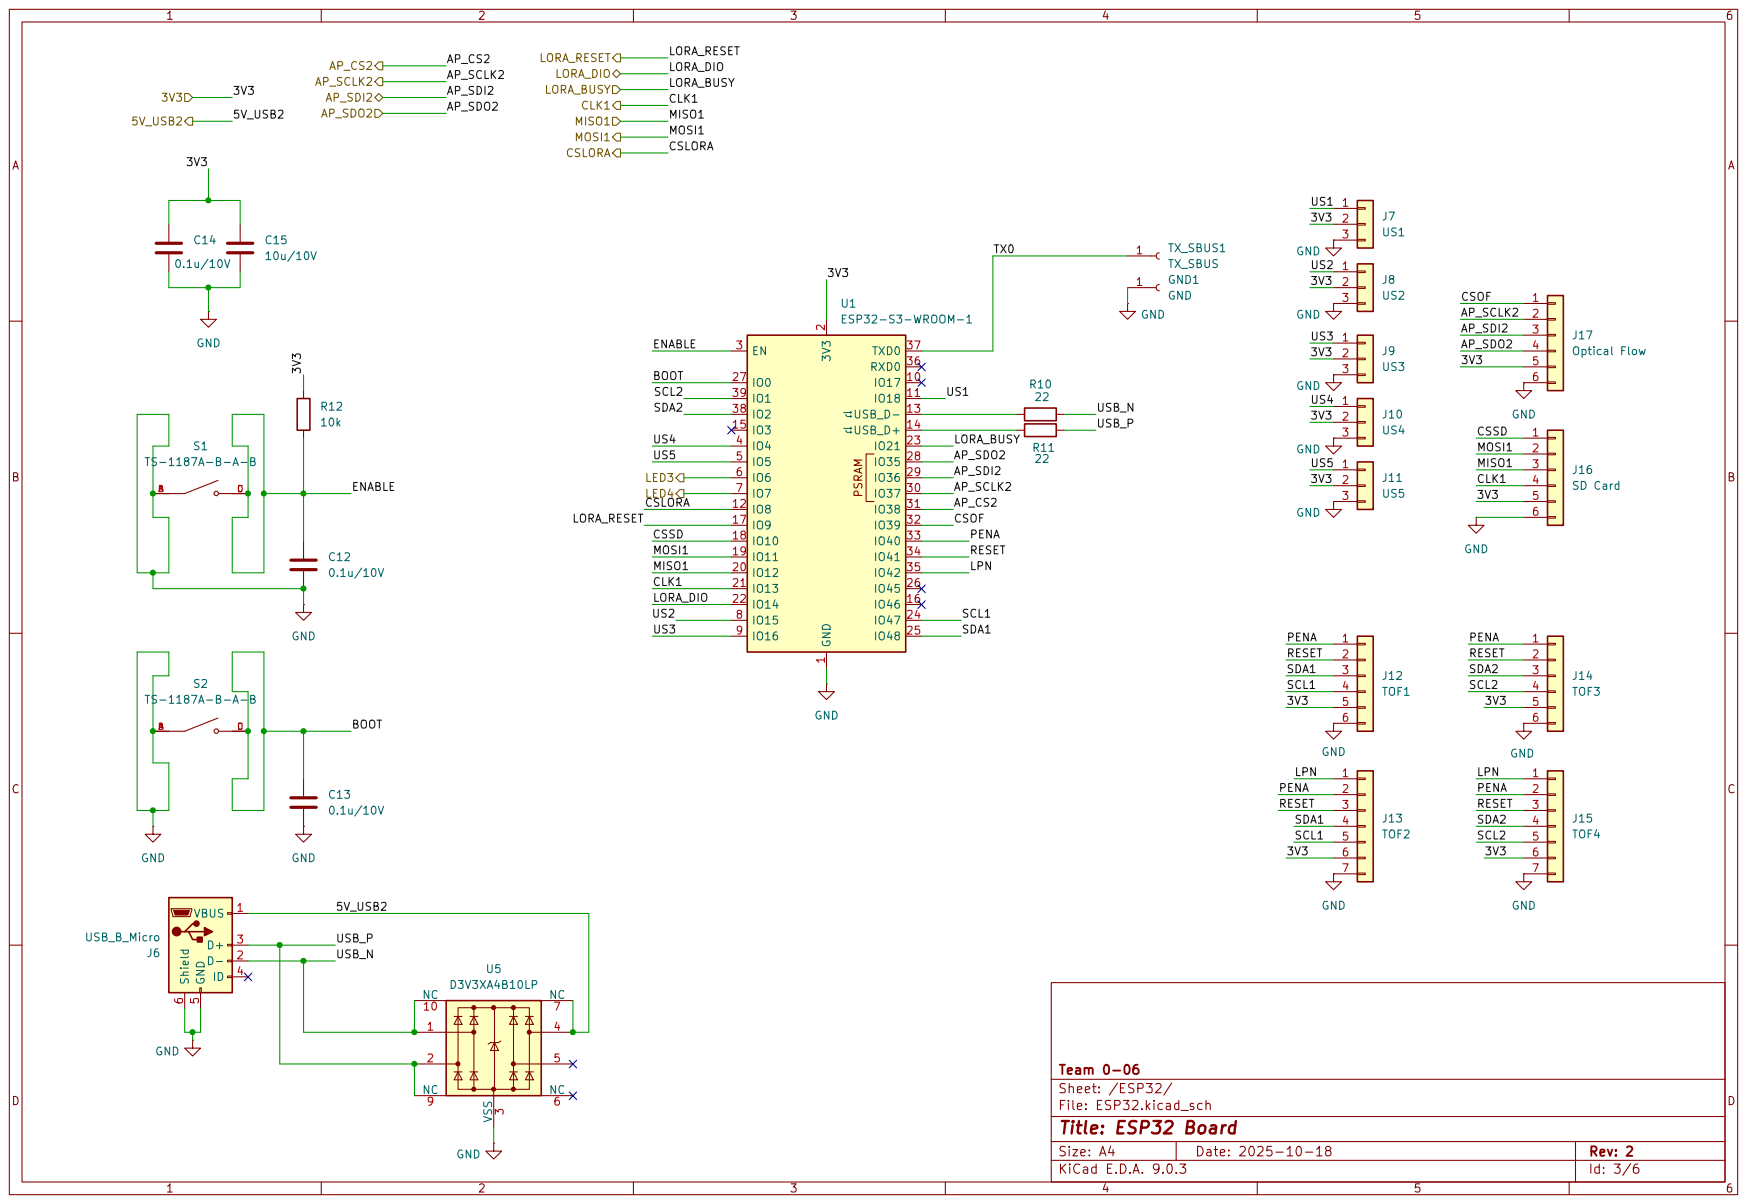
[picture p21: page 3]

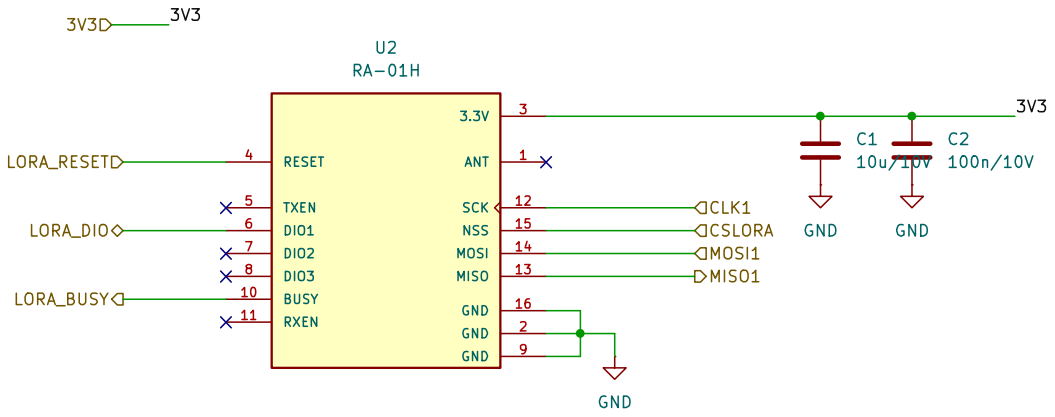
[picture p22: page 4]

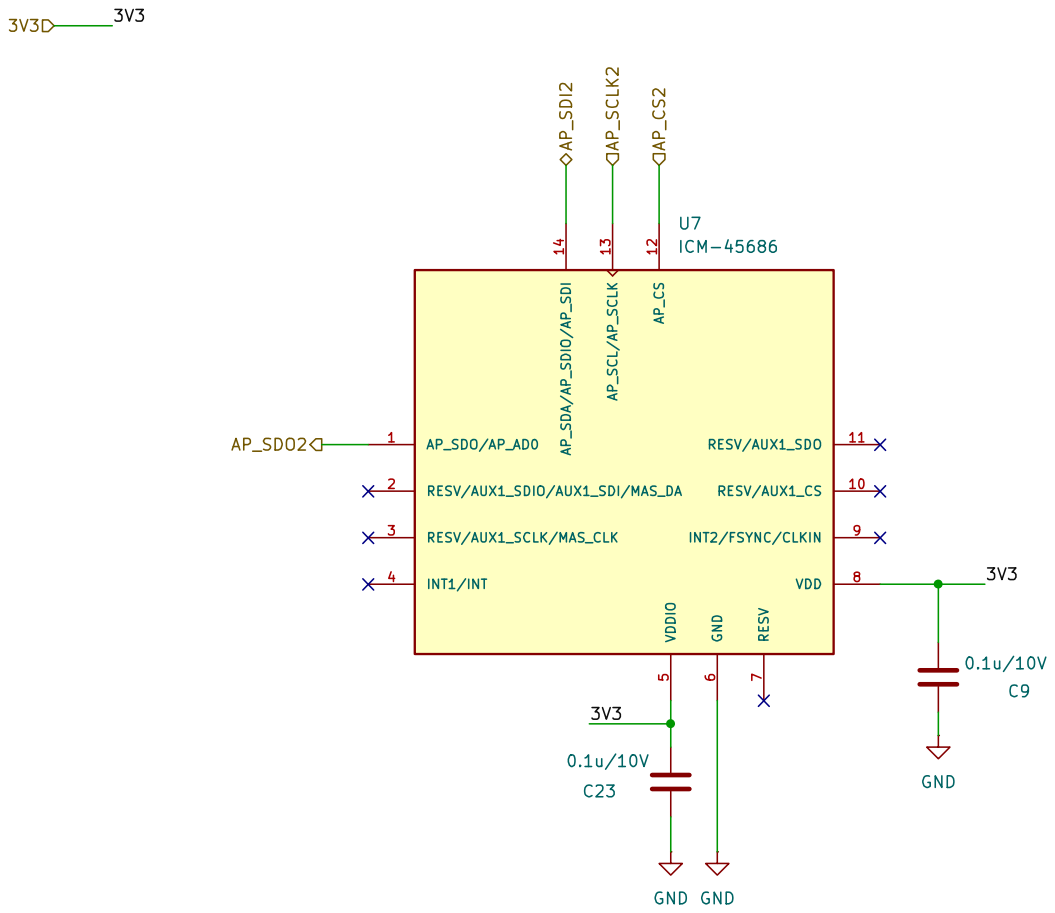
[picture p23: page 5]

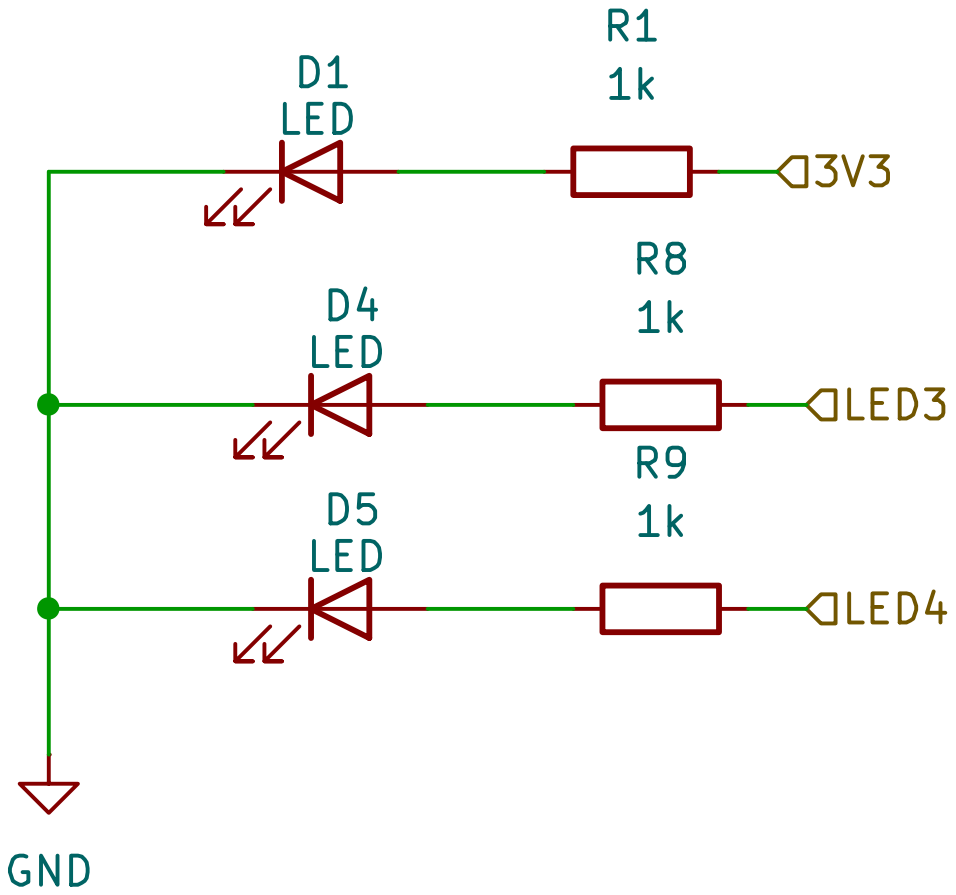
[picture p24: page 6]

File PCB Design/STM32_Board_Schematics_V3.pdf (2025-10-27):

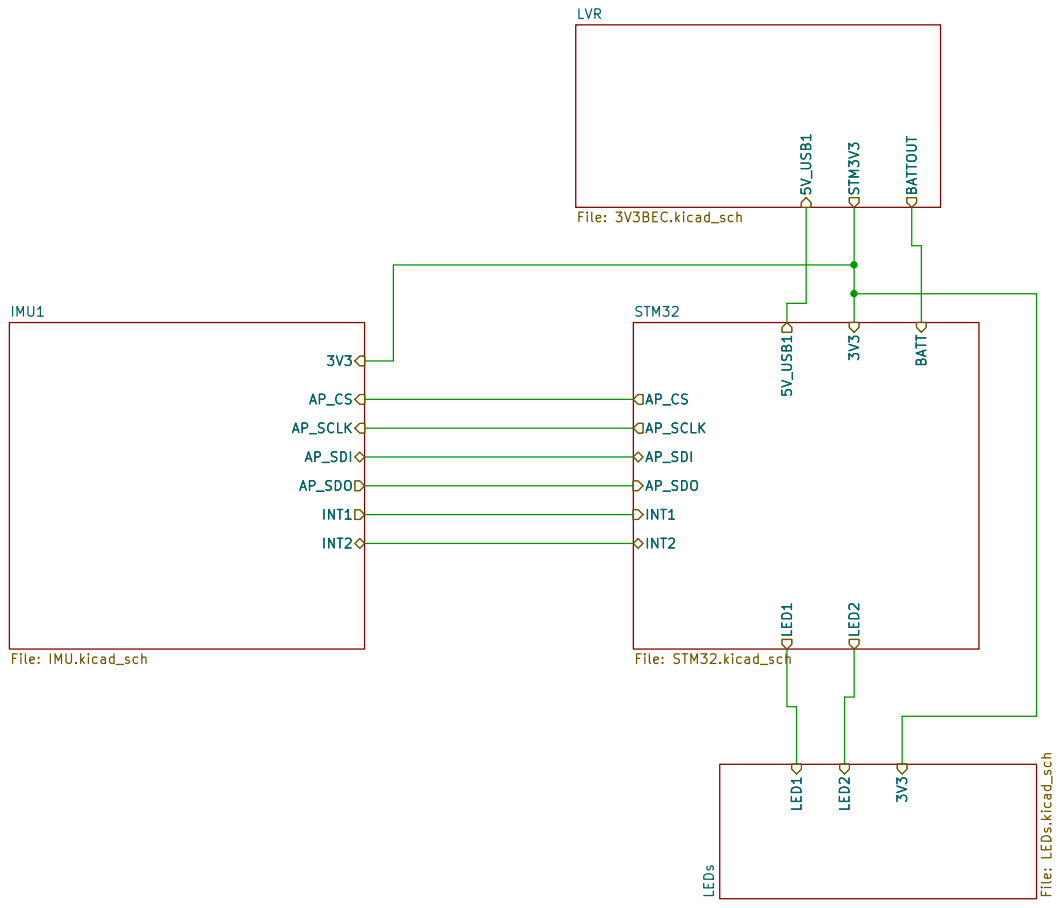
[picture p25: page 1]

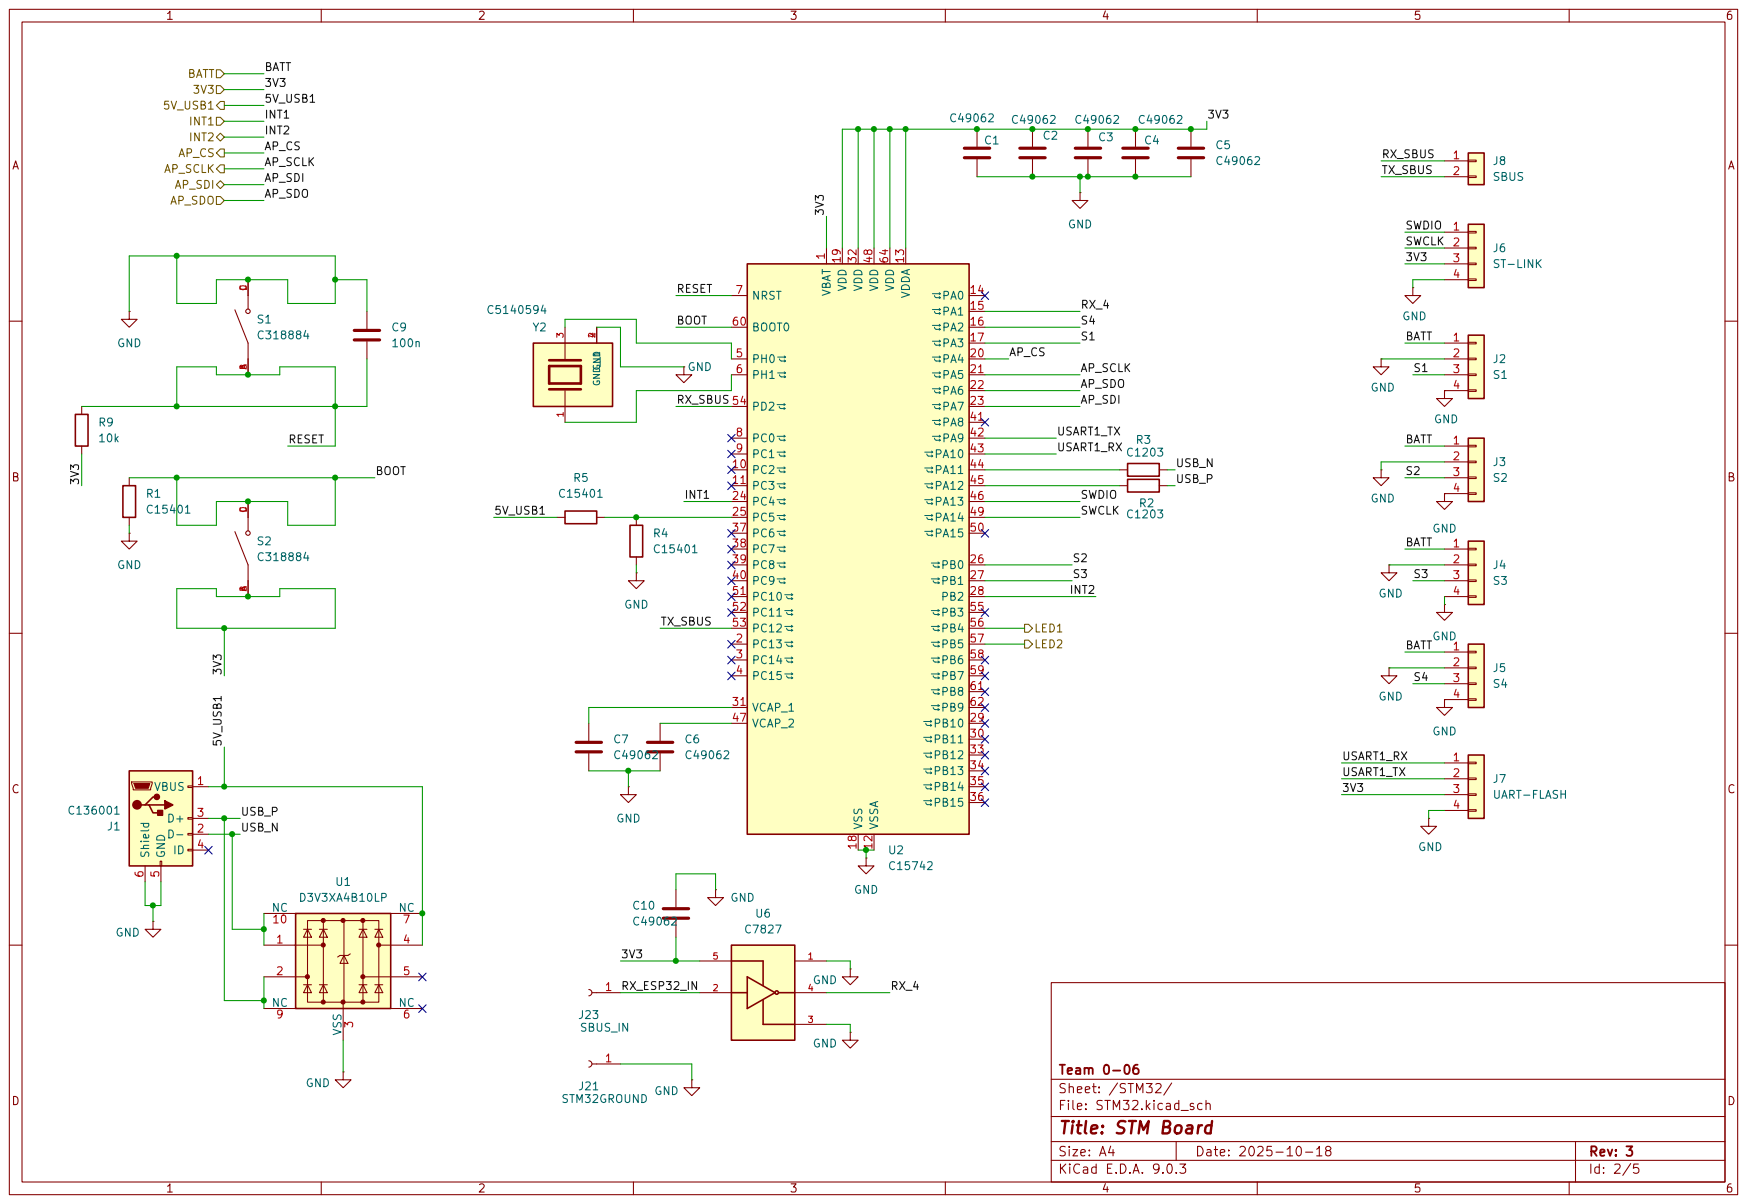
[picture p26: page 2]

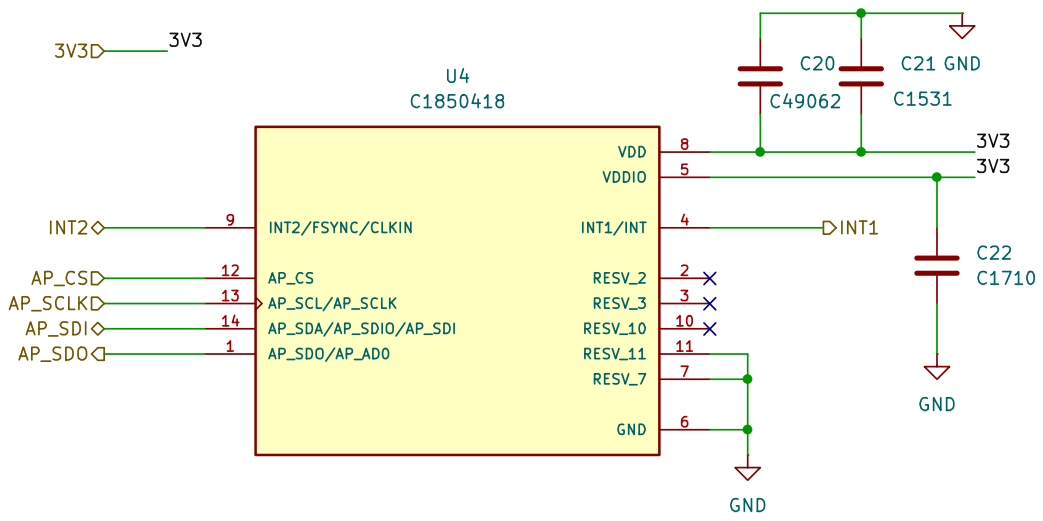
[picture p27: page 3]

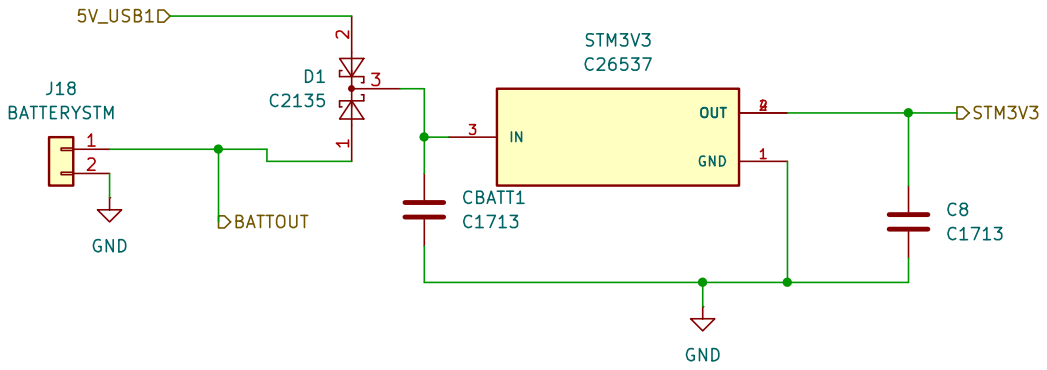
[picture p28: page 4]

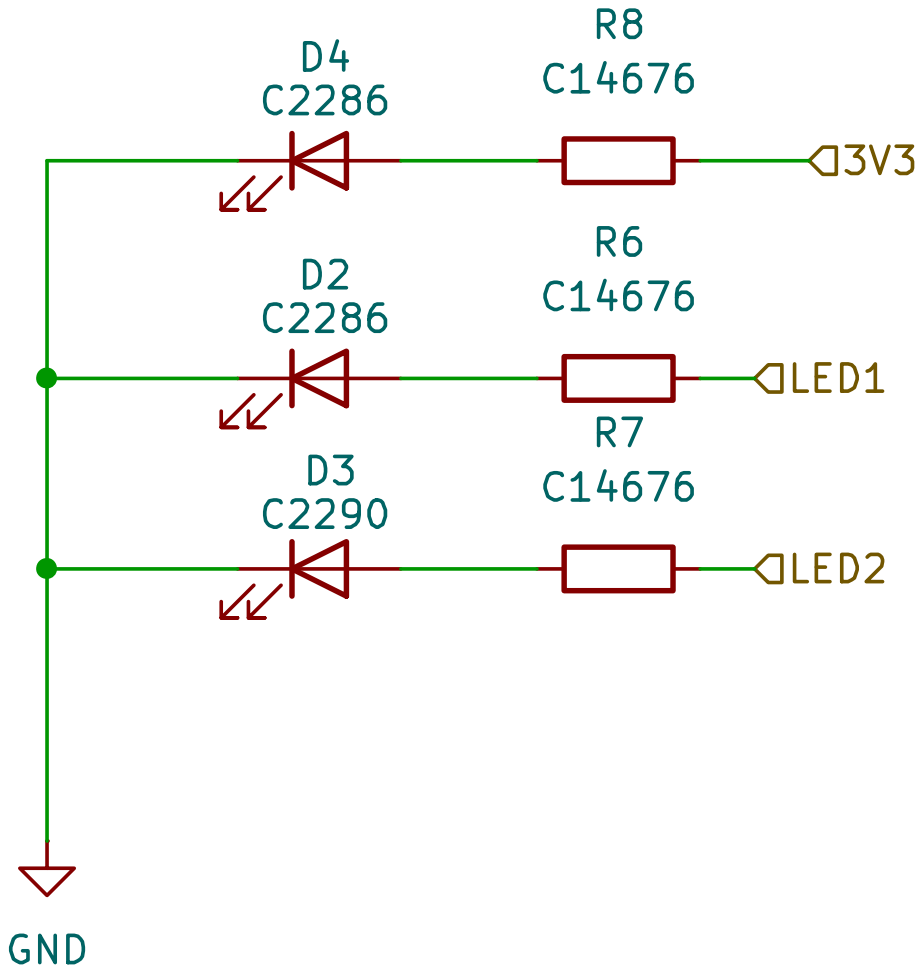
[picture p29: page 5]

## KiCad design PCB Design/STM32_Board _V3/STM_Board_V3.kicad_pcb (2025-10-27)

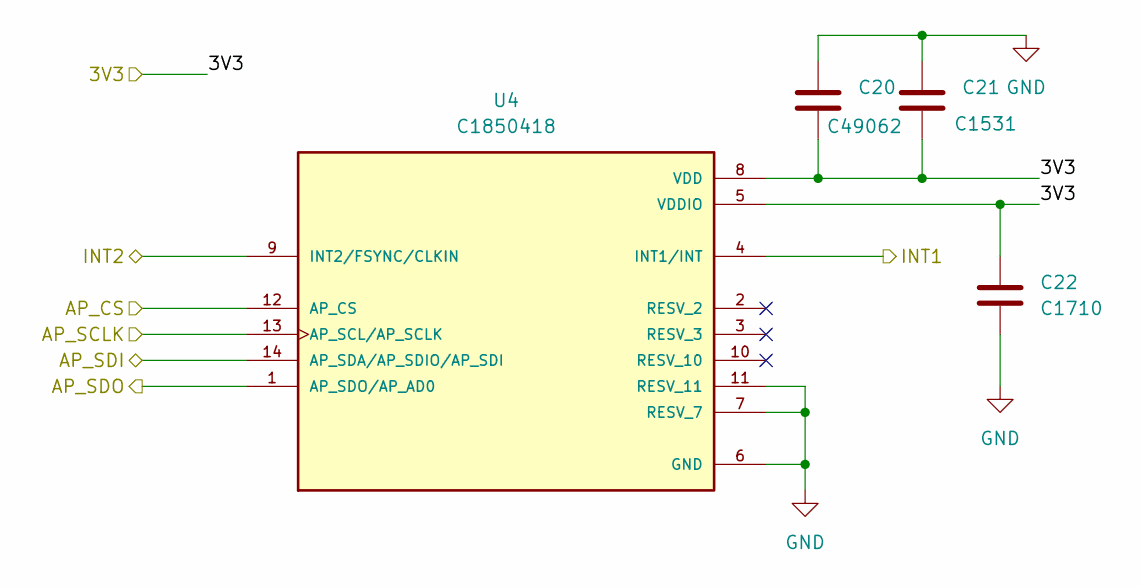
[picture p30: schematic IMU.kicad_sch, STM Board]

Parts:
C20: C49062; C_0402_1005Metric
C21: C1531; C_0603_1608Metric
C22: C1710; C_0805_2012Metric
U4: C1850418; PQFN50P300X250X97-14N; PARTREV 1.2

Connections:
/IMU1/3V3: C20.2, C21.2, C22.1, U4.5 (VDDIO), U4.8 (VDD); also elsewhere on the board
/STM32/AP_CS: U4.12 (AP_CS); also elsewhere on the board
/STM32/AP_SCLK: U4.13 (AP_SCL/AP_SCLK); also elsewhere on the board
/STM32/AP_SDI: U4.14 (AP_SDA/AP_SDIO/AP_SDI); also elsewhere on the board
/STM32/AP_SDO: U4.1 (AP_SDO/AP_AD0); also elsewhere on the board
/STM32/INT1: U4.4 (INT1/INT); also elsewhere on the board
/STM32/INT2: U4.9 (INT2/FSYNC/CLKIN); also elsewhere on the board
GND: C20.1, C21.1, C22.2, U4.6 (GND), U4.7 (RESV_7), U4.11 (RESV_11); also elsewhere on the board

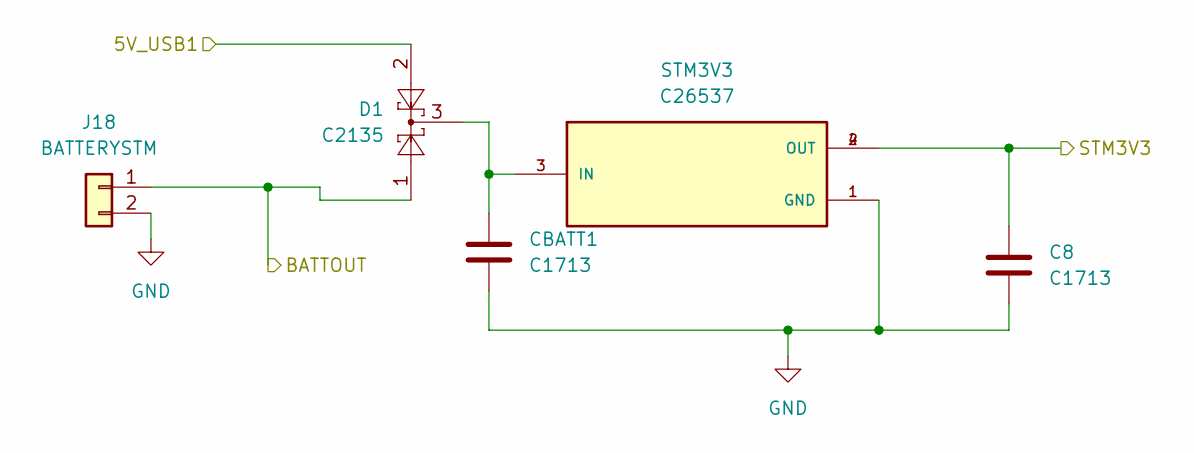
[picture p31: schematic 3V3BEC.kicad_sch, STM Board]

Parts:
C8: C1713; C_0805_2012Metric
CBATT1: C1713; C_0805_2012Metric
D1: C2135; SOT-23
J18: BATTERYSTM; 2_SolderPad_2mm
STM3V3: C26537; SOT230P700X180-4N; DigiKey_Part_Number NCP1117ST33T3GOSCT-ND

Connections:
/IMU1/3V3: C8.1, STM3V3.2 (OUT), STM3V3.4 (OUT); also elsewhere on the board
/STM32/5V_USB1: D1.2; also elsewhere on the board
/STM32/BATT: D1.1, J18.1; also elsewhere on the board
GND: C8.2, CBATT1.2, J18.2, STM3V3.1 (GND); also elsewhere on the board
unnamed: CBATT1.1, D1.3, STM3V3.3 (IN)

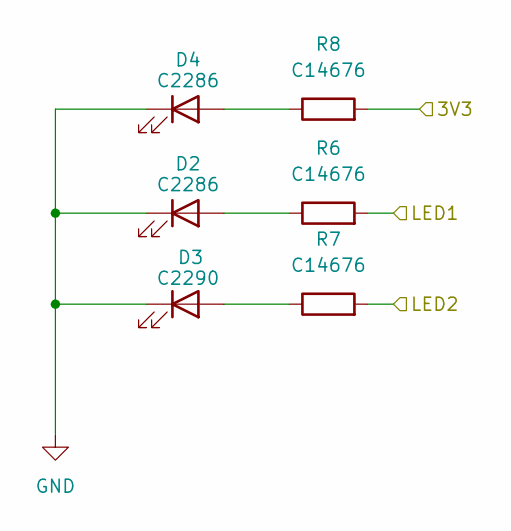
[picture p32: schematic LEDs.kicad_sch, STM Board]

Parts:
D2, D4: C2286; LED_0603_1608Metric
D3: C2290; LED_0603_1608Metric
R6, R7, R8: C14676; R_0603_1608Metric

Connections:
/IMU1/3V3: R8.2; also elsewhere on the board
/LEDs/LED1: R6.2; also elsewhere on the board
/LEDs/LED2: R7.2; also elsewhere on the board
GND: D2.1 (K), D3.1 (K), D4.1 (K); also elsewhere on the board
unnamed: D2.2 (A), R6.1
unnamed: D3.2 (A), R7.1
unnamed: D4.2 (A), R8.1

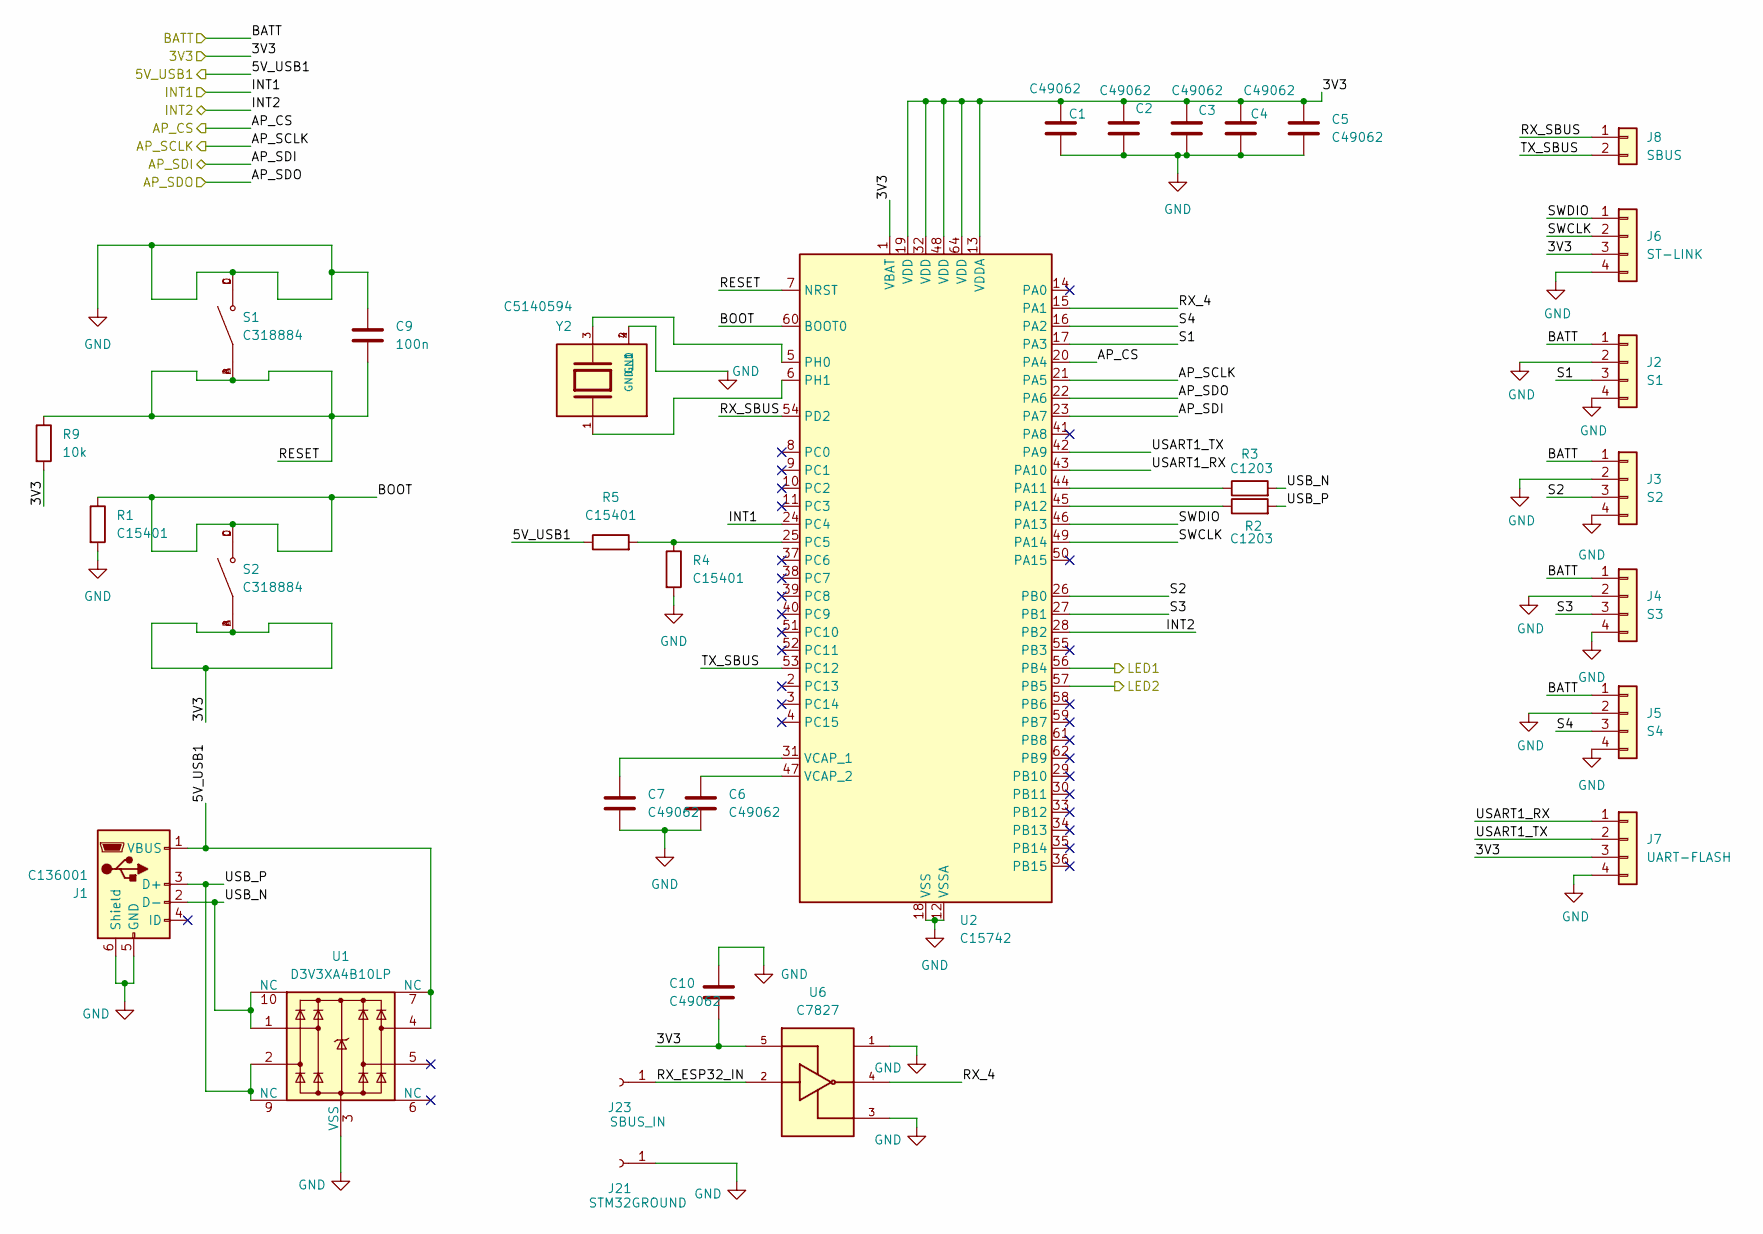
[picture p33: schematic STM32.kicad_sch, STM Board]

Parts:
C1, C2, C3, C4, C5, C6, C7, C10: C49062; C_0402_1005Metric
C9: 100n; C_0402_1005Metric
J1: C136001; USB_Micro-B_Amphenol_10103594-0001LF_Horizontal
J2: S1; 4_SolderPad_2mm
J3: S2; 4_SolderPad_2mm
J4: S3; 4_SolderPad_2mm
J5: S4; 4_SolderPad_2mm
J6: ST-LINK; 4_SolderPad_2mm
J7: UART-FLASH; 4_SolderPad_2mm
J8: SBUS; 2_SolderPad_2mm
J21: STM32GROUND; SolderPad_2mm
J23: SBUS_IN; SolderPad_2mm
R1, R4, R5: C15401; R_0603_1608Metric
R2, R3: C1203; R_0603_1608Metric
R9: 10k; R_0603_1608Metric
S1, S2: C318884; SW_TS-1187A-B-A-B; PARTREV A0
U1: D3V3XA4B10LP; Diodes_UDFN-10_1.0x2.5mm_P0.5mm
U2: C15742; LQFP-64_10x10mm_P0.5mm
U6: C7827; SOT95P280X145-5N; PARTREV AD
Y2: C5140594; XTAL_ABM8AIG-8.000MHZ-1Z-T; PARTREV 43629

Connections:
/IMU1/3V3: C1.1, C2.1, C3.1, C4.1, C5.1, C10.2, J6.3, J7.3, R9.2, S2.A, S2.B, U2.1 (VBAT), U2.13 (VDDA), U2.19 (VDD), U2.32 (VDD), U2.48 (VDD), U2.64 (VDD), U6.5; also elsewhere on the board
/LEDs/LED1: U2.56 (PB4); also elsewhere on the board
/LEDs/LED2: U2.57 (PB5); also elsewhere on the board
/STM32/5V_USB1: J1.1 (VBUS), R5.1, U1.4, U1.7 (NC); also elsewhere on the board
/STM32/AP_CS: U2.20 (PA4); also elsewhere on the board
/STM32/AP_SCLK: U2.21 (PA5); also elsewhere on the board
/STM32/AP_SDI: U2.23 (PA7); also elsewhere on the board
/STM32/AP_SDO: U2.22 (PA6); also elsewhere on the board
/STM32/BATT: J2.1, J3.1, J4.1, J5.1; also elsewhere on the board
/STM32/BOOT: R1.1, S2.C, S2.D, U2.60 (BOOT0)
/STM32/INT1: U2.24 (PC4); also elsewhere on the board
/STM32/INT2: U2.28 (PB2); also elsewhere on the board
/STM32/RESET: C9.2, R9.1, S1.A, S1.B, U2.7 (NRST)
/STM32/RX_4: U2.15 (PA1), U6.4
/STM32/RX_ESP32_IN: J23.1, U6.2
/STM32/RX_SBUS: J8.1, U2.54 (PD2)
/STM32/S1: J2.3, U2.17 (PA3)
/STM32/S2: J3.3, U2.26 (PB0)
/STM32/S3: J4.3, U2.27 (PB1)
/STM32/S4: J5.3, U2.16 (PA2)
/STM32/SWCLK: J6.2, U2.49 (PA14)
/STM32/SWDIO: J6.1, U2.46 (PA13)
/STM32/TX_SBUS: J8.2, U2.53 (PC12)
/STM32/USART1_RX: J7.1, U2.43 (PA10)
/STM32/USART1_TX: J7.2, U2.42 (PA9)
/STM32/USB_N: J1.2 (D-), R3.2, U1.1, U1.10 (NC)
/STM32/USB_P: J1.3 (D+), R2.2, U1.2, U1.9 (NC)
GND: C1.2, C2.2, C3.2, C4.2, C5.2, C6.2, C7.2, C9.1, C10.1, J1.5 (GND), J1.6 (Shield), J2.2, J2.4, J3.2, J3.4, J4.2, J4.4, J5.2, J5.4, J6.4, J7.4, J21.1, R1.2, R4.2, S1.C, S1.D, U1.3 (VSS), U1.8 (VSS), U2.12 (VSSA), U2.18 (VSS), U2.63 (VSS), U6.1, U6.3, Y2.2 (GND), Y2.4 (GND__1); also elsewhere on the board
unnamed: R3.1, U2.44 (PA11)
unnamed: R2.1, U2.45 (PA12)
unnamed: R4.1, R5.2, U2.25 (PC5)
unnamed: U2.5 (PH0), Y2.3
unnamed: U2.6 (PH1), Y2.1
unnamed: C7.1, U2.31 (VCAP_1)
unnamed: C6.1, U2.47 (VCAP_2)

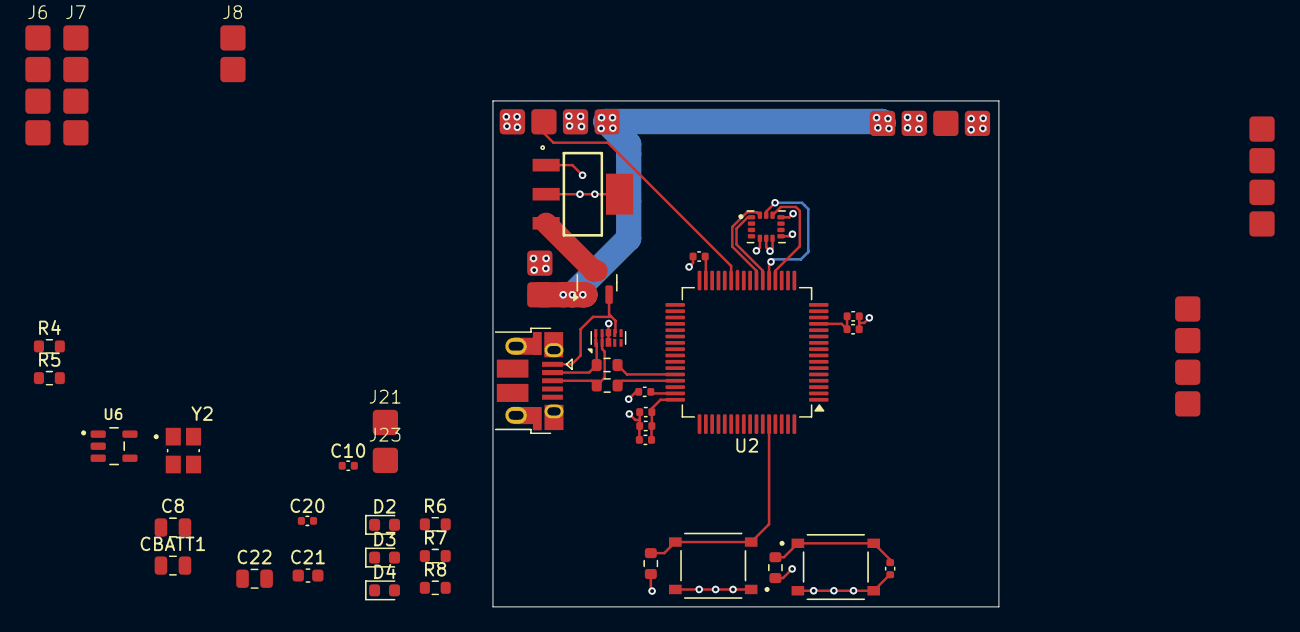
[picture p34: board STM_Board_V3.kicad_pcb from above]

Board: 4 copper layers, 40.0 x 40.0 mm, 46 parts (0 on the bottom side), 39 nets.

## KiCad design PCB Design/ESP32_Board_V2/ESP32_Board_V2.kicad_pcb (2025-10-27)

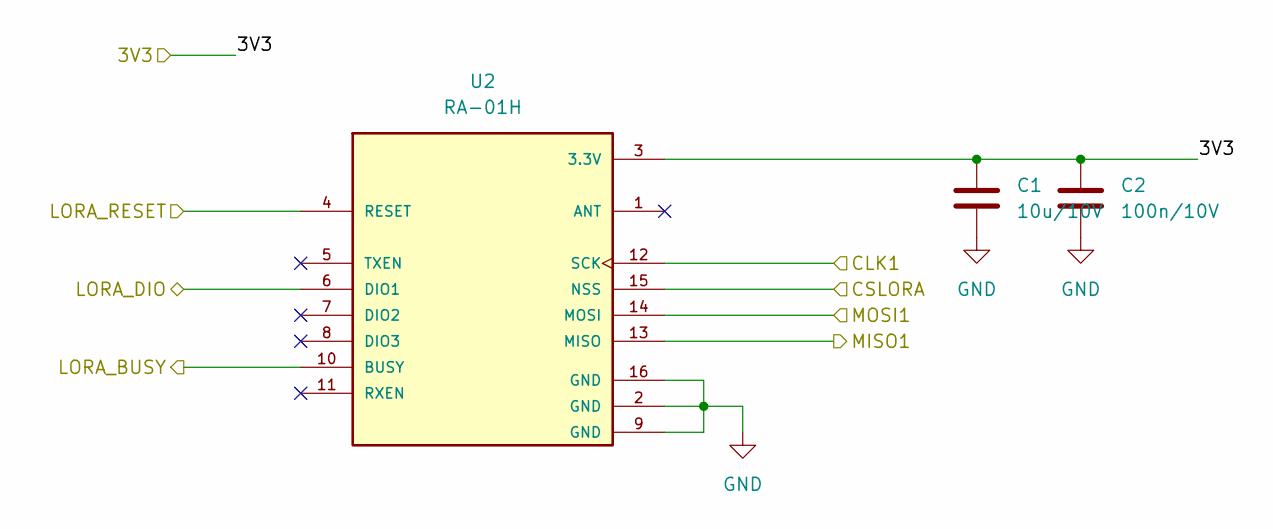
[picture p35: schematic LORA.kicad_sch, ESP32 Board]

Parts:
C1: 10u/10V; C_0805_2012Metric
C2: 100n/10V; C_0402_1005Metric
U2: RA-01H; XCVR_RA-01H; PARTREV V1.0

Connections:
/ESP32/3V3: C1.1, C2.1, U2.3 (3.3V); also elsewhere on the board
/ESP32/CLK1: U2.12 (SCK); also elsewhere on the board
/ESP32/CSLORA: U2.15 (NSS); also elsewhere on the board
/ESP32/LORA_BUSY: U2.10 (BUSY); also elsewhere on the board
/ESP32/LORA_DIO: U2.6 (DIO1); also elsewhere on the board
/ESP32/LORA_RESET: U2.4 (RESET); also elsewhere on the board
/ESP32/MISO1: U2.13 (MISO); also elsewhere on the board
/ESP32/MOSI1: U2.14 (MOSI); also elsewhere on the board
GND: C1.2, C2.2, U2.2 (GND), U2.9 (GND), U2.16 (GND); also elsewhere on the board

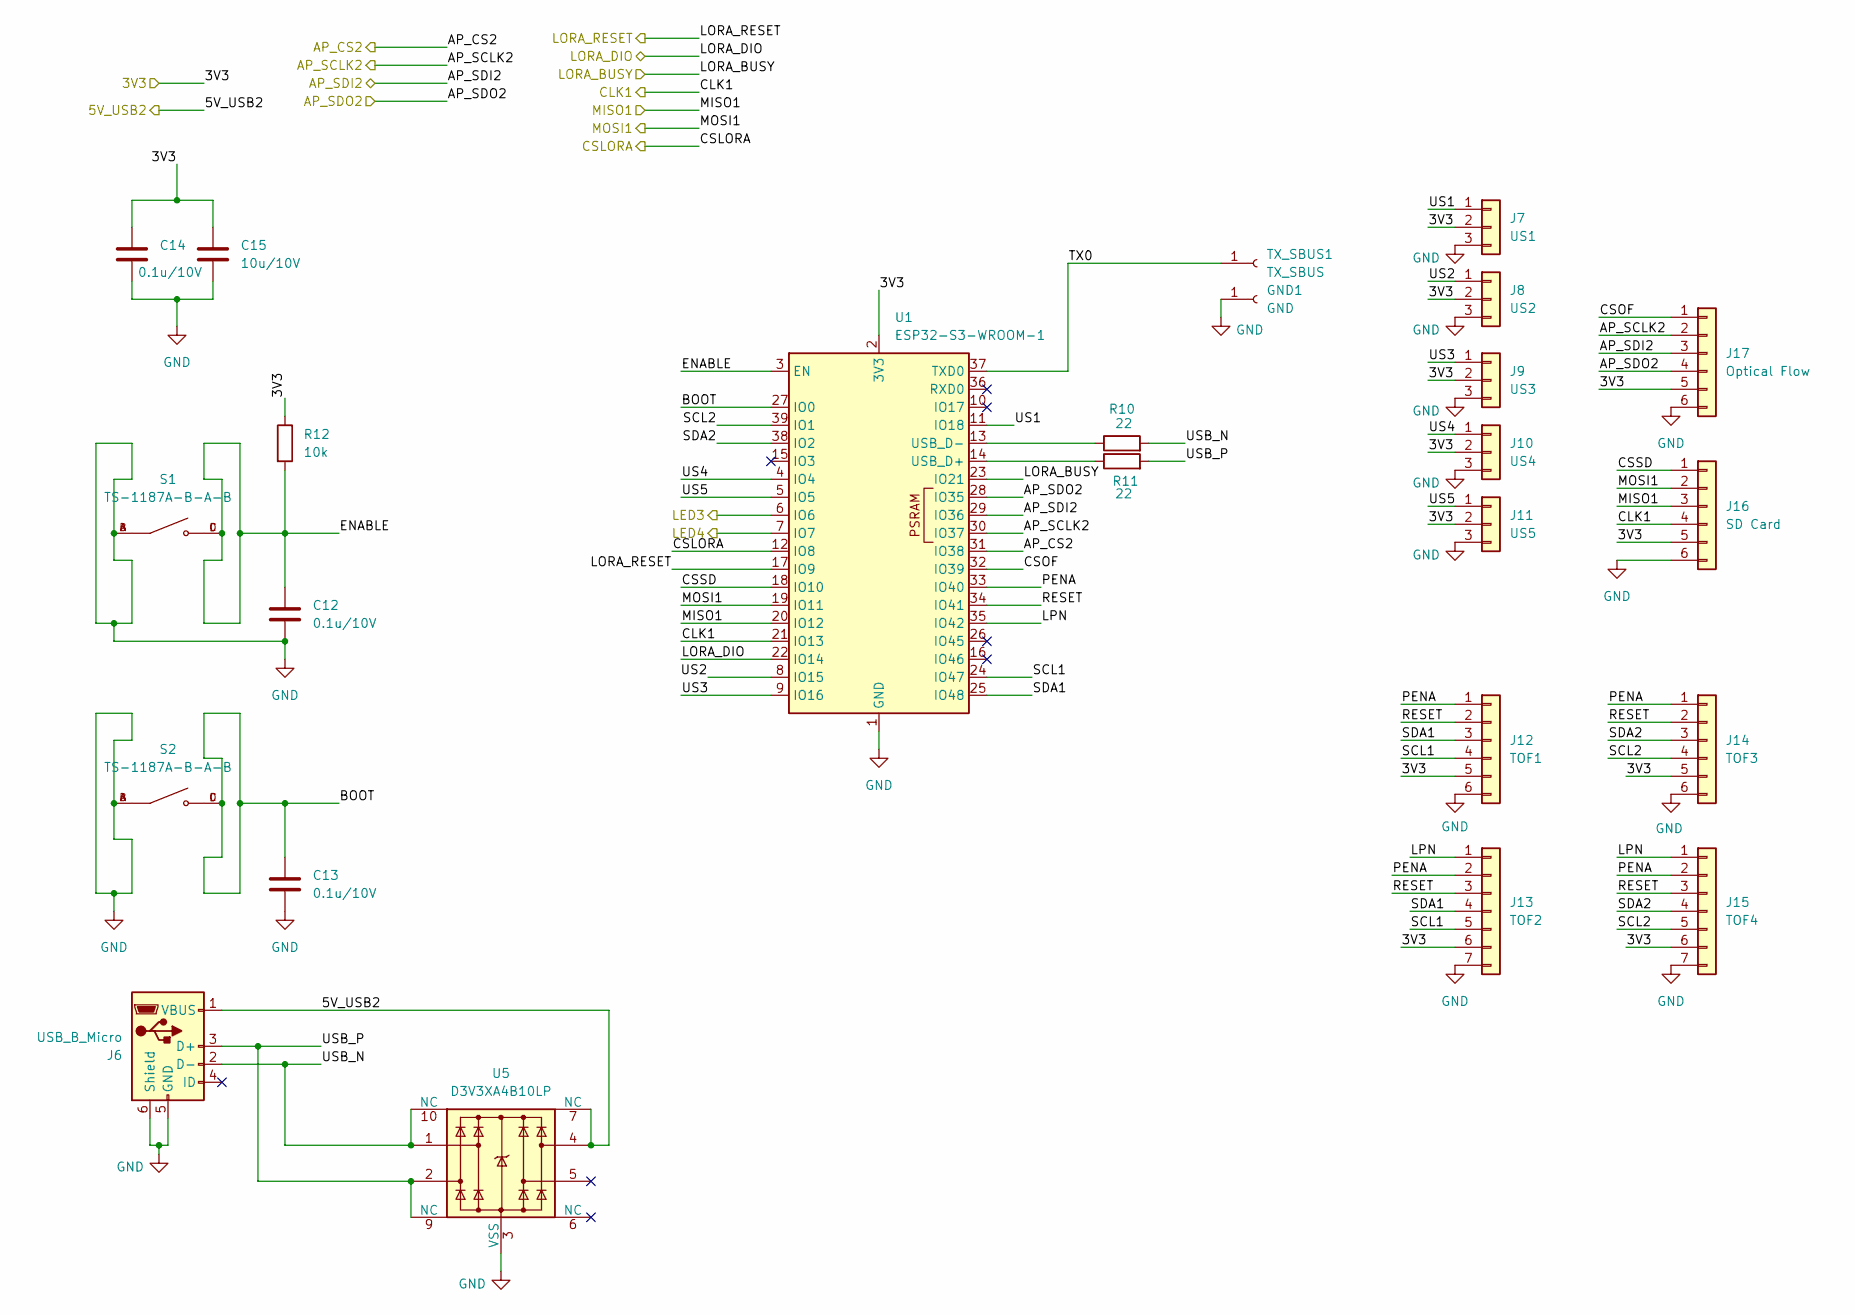
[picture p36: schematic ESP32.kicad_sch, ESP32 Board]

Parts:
C12, C13, C14: 0.1u/10V; C_0402_1005Metric
C15: 10u/10V; C_0805_2012Metric
GND1: GND; SolderPad_2mm
J6: USB_B_Micro; USB_Micro-B_Amphenol_10103594-0001LF_Horizontal
J7: US1; PinHeader_1x03_P1.27mm_Vertical
J8: US2; PinHeader_1x03_P1.27mm_Vertical
J9: US3; PinHeader_1x03_P1.27mm_Vertical
J10: US4; PinHeader_1x03_P1.27mm_Vertical
J11: US5; PinHeader_1x03_P1.27mm_Vertical
J12: TOF1; PinHeader_1x06_P1.27mm_Vertical
J13: TOF2; PinHeader_1x07_P1.27mm_Vertical
J14: TOF3; PinHeader_1x06_P1.27mm_Vertical
J15: TOF4; PinHeader_1x07_P1.27mm_Vertical
J16: SD Card; PinHeader_1x06_P1.27mm_Vertical
J17: Optical Flow; PinHeader_1x06_P1.27mm_Vertical
R10, R11: 22; R_0603_1608Metric
R12: 10k; R_0603_1608Metric
S1, S2: TS-1187A-B-A-B; SW_TS-1187A-B-A-B; PARTREV A0
TX_SBUS1: TX_SBUS; SolderPad_2mm
U1: ESP32-S3-WROOM-1; ESP32-S3-WROOM-1U
U5: D3V3XA4B10LP; Diodes_UDFN-10_1.0x2.5mm_P0.5mm

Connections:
/ESP32/3V3: C14.1, C15.1, J7.2, J8.2, J9.2, J10.2, J11.2, J12.5, J13.6, J14.5, J15.6, J16.5, J17.5, R12.1, U1.2 (3V3); also elsewhere on the board
/ESP32/5V_USB2: J6.1 (VBUS), U5.4, U5.7 (NC); also elsewhere on the board
/ESP32/AP_CS2: U1.31 (IO38); also elsewhere on the board
/ESP32/AP_SCLK2: J17.2, U1.30 (IO37); also elsewhere on the board
/ESP32/AP_SDI2: J17.3, U1.29 (IO36); also elsewhere on the board
/ESP32/AP_SDO2: J17.4, U1.28 (IO35); also elsewhere on the board
/ESP32/BOOT: C13.1, S2.C, S2.D, U1.27 (IO0)
/ESP32/CLK1: J16.4, U1.21 (IO13); also elsewhere on the board
/ESP32/CSLORA: U1.12 (IO8); also elsewhere on the board
/ESP32/CSOF: J17.1, U1.32 (IO39)
/ESP32/CSSD: J16.1, U1.18 (IO10)
/ESP32/ENABLE: C12.1, R12.2, S1.C, S1.D, U1.3 (EN)
/ESP32/LED3: U1.6 (IO6); also elsewhere on the board
/ESP32/LED4: U1.7 (IO7); also elsewhere on the board
/ESP32/LORA_BUSY: U1.23 (IO21); also elsewhere on the board
/ESP32/LORA_DIO: U1.22 (IO14); also elsewhere on the board
/ESP32/LORA_RESET: U1.17 (IO9); also elsewhere on the board
/ESP32/LPN: J13.1, J15.1, U1.35 (IO42)
/ESP32/MISO1: J16.3, U1.20 (IO12); also elsewhere on the board
/ESP32/MOSI1: J16.2, U1.19 (IO11); also elsewhere on the board
/ESP32/PENA: J12.1, J13.2, J14.1, J15.2, U1.33 (IO40)
/ESP32/RESET: J12.2, J13.3, J14.2, J15.3, U1.34 (IO41)
/ESP32/SCL1: J12.4, J13.5, U1.24 (IO47)
/ESP32/SCL2: J14.4, J15.5, U1.39 (IO1)
/ESP32/SDA1: J12.3, J13.4, U1.25 (IO48)
/ESP32/SDA2: J14.3, J15.4, U1.38 (IO2)
/ESP32/TX0: TX_SBUS1.1, U1.37 (TXD0)
/ESP32/US1: J7.1, U1.11 (IO18)
/ESP32/US2: J8.1, U1.8 (IO15)
/ESP32/US3: J9.1, U1.9 (IO16)
/ESP32/US4: J10.1, U1.4 (IO4)
/ESP32/US5: J11.1, U1.5 (IO5)
/ESP32/USB_N: J6.2 (D-), R10.2, U5.1, U5.10 (NC)
/ESP32/USB_P: J6.3 (D+), R11.2, U5.2, U5.9 (NC)
GND: C12.2, C13.2, C14.2, C15.2, GND1.1, J6.5 (GND), J6.6 (Shield), J7.3, J8.3, J9.3, J10.3, J11.3, J12.6, J13.7, J14.6, J15.7, J16.6, J17.6, S1.A, S1.B, S2.A, S2.B, U1.1 (GND), U1.40 (GND), U1.41 (GND), U5.3 (VSS), U5.8 (VSS); also elsewhere on the board
unnamed: R11.1, U1.14 (USB_D+)
unnamed: R10.1, U1.13 (USB_D-)

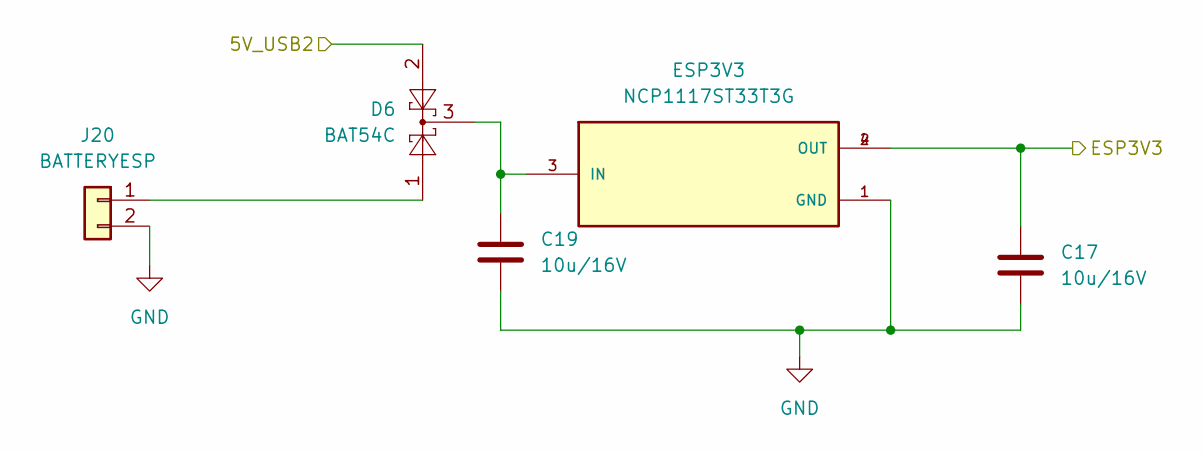
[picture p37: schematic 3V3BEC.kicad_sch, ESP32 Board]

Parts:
C17, C19: 10u/16V; C_0805_2012Metric
D6: BAT54C; SOT-23
ESP3V3: NCP1117ST33T3G; SOT230P700X180-4N; DigiKey_Part_Number NCP1117ST33T3GOSCT-ND
J20: BATTERYESP; 2_SolderPad_2mm

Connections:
/ESP32/3V3: C17.1, ESP3V3.2 (OUT), ESP3V3.4 (OUT); also elsewhere on the board
/ESP32/5V_USB2: D6.2; also elsewhere on the board
GND: C17.2, C19.2, ESP3V3.1 (GND), J20.2; also elsewhere on the board
unnamed: C19.1, D6.3, ESP3V3.3 (IN)
unnamed: D6.1, J20.1

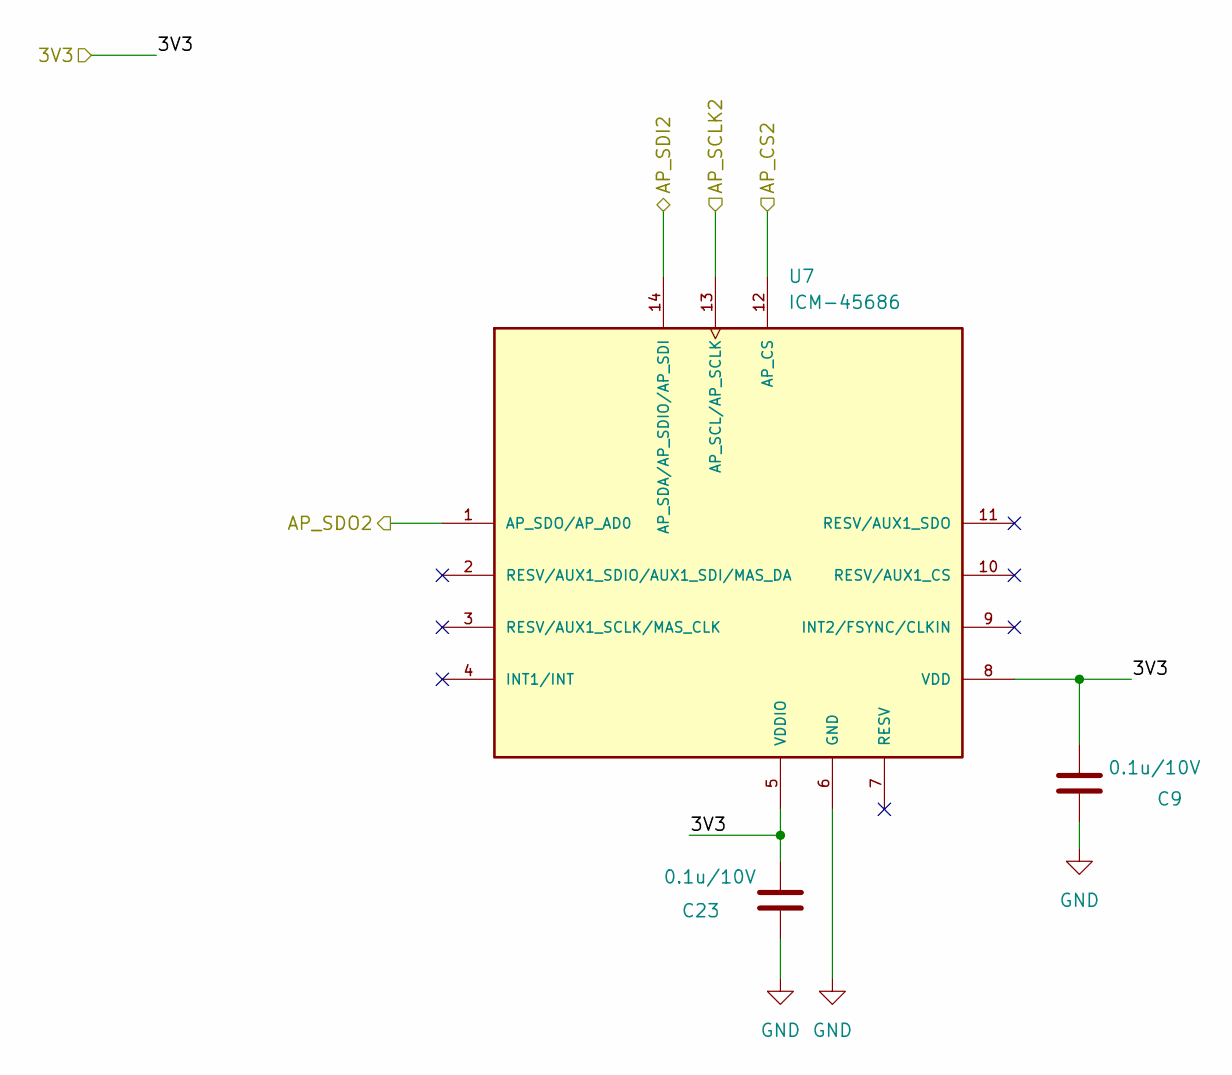
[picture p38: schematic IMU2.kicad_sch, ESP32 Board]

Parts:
C9, C23: 0.1u/10V; C_0402_1005Metric
U7: ICM-45686; IC_ICM-45686; PARTREV 0.2

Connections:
/ESP32/3V3: C9.2, C23.2, U7.5 (VDDIO), U7.8 (VDD); also elsewhere on the board
/ESP32/AP_CS2: U7.12 (AP_CS); also elsewhere on the board
/ESP32/AP_SCLK2: U7.13 (AP_SCL/AP_SCLK); also elsewhere on the board
/ESP32/AP_SDI2: U7.14 (AP_SDA/AP_SDIO/AP_SDI); also elsewhere on the board
/ESP32/AP_SDO2: U7.1 (AP_SDO/AP_AD0); also elsewhere on the board
GND: C9.1, C23.1, U7.6 (GND); also elsewhere on the board

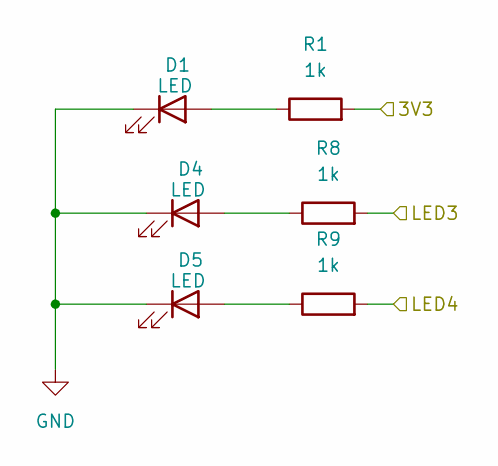
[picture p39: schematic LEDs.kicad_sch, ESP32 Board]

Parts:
D1, D4, D5: LED; LED_0603_1608Metric
R1, R8, R9: 1k; R_0603_1608Metric

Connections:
/ESP32/3V3: R1.2; also elsewhere on the board
/ESP32/LED3: R8.2; also elsewhere on the board
/ESP32/LED4: R9.2; also elsewhere on the board
GND: D1.1 (K), D4.1 (K), D5.1 (K); also elsewhere on the board
unnamed: D1.2 (A), R1.1
unnamed: D4.2 (A), R8.1
unnamed: D5.2 (A), R9.1

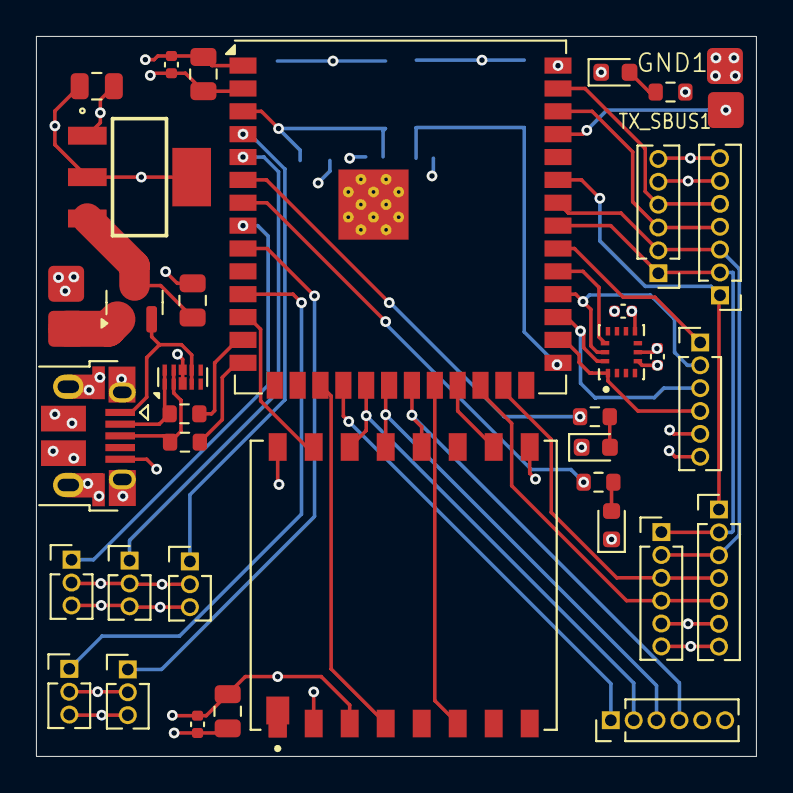
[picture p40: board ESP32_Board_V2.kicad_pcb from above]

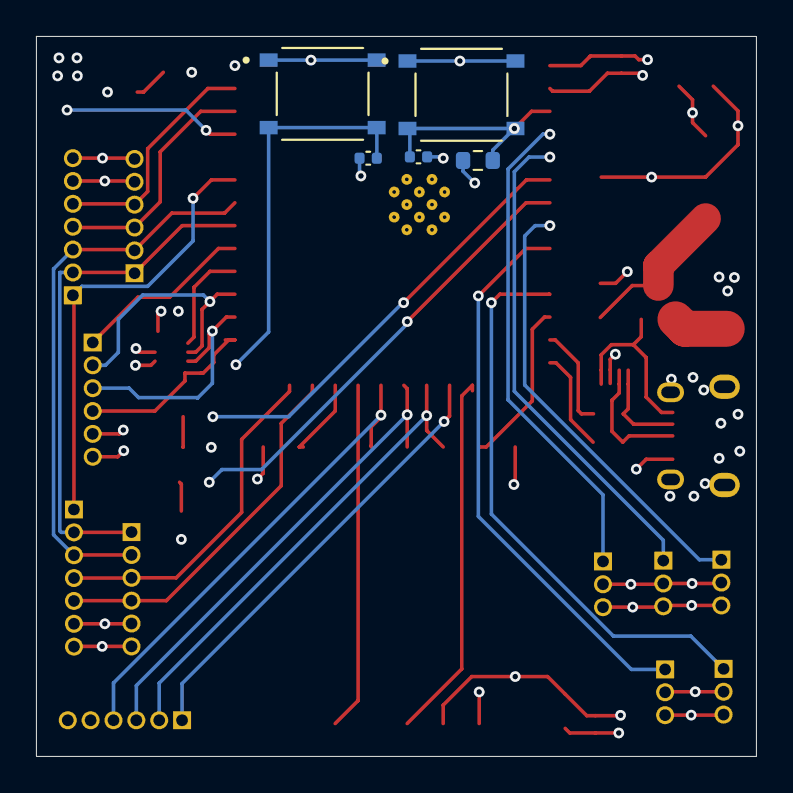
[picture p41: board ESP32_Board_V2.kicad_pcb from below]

Board: 4 copper layers, 40.0 x 40.0 mm, 42 parts (5 on the bottom side), 42 nets.

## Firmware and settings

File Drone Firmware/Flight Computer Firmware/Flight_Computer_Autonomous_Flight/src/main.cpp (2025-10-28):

#include <Arduino.h>
#include <Ticker.h>

#include "SBUS.h"
#include "LoRa_SX1262.h"

#include <Wire.h>
#include <SparkFun_VL53L5CX_Library.h> //http://librarymanager/All#SparkFun_VL53L5CX

#define Ultrasonic_Rx_initialiser 40 // Rx Front US to initialise ultrasonic sensors'

#define pwPinTop 15  // Top US
volatile unsigned long pulseStart1 = 0;
volatile double distanceCm1 = 0;
volatile bool US_ready1 = false;
volatile double CurrentDistance = 0; // read from ultrasonic

#define pwPinFront 4  // Front US
volatile unsigned long pulseStartF = 0;
volatile double distanceCmF = 0;
volatile bool US_readyF = false;
volatile double CurrentDistanceF = 0; // read from ultrasonic


#define pwPinLeftUS  5 // LEFT US
volatile unsigned long pulseStartL = 0;
volatile double distanceCmL = 0;
volatile bool US_readyL = false;
volatile double CurrentDistance_US_L = 0; // read from ultrasonic

// Sensor objects and measurement data
SparkFun_VL53L5CX sensor1;
VL53L5CX_ResultsData measurementData1; // Result data class structure, 1356 byes of RAM
int imageResolution1 = 0;
int imageWidth1 = 0;
int frontAvg = -1;
int backAvg = -1;
int totalAvg = -1;

// TOF RIGHT
#define SDA_PIN 48
#define SCL_PIN 47


static RadioEvents_t RadioEvents;
hw_config hwConfig;
time_t lastMessage;

Ticker loraTimer;
Ticker SBUSTimer;

#define FAILSAFE_LORA_TIMEOUT 30000 // 30 secs
#define HOVER_LORA_TIMEOUT 10000     // 5 secs
#define LORA_TIMER_UDPATE_RATE 1000 // check every 1000 ms

// Using UART0 on ESP32-S3
#define RX_PIN 44
#define TX_PIN 43

#define THROTTLE_MIN 890
#define THROTTLE_MID 1445
#define THROTTLE_MAX 2000 // shrink range of throttle

uint8_t sbusPacket[SBUS_PACKET_LENGTH];
int rcChannels[SBUS_CHANNEL_NUMBER];
uint32_t sbusTime = 0;

// Timing variables
uint32_t currentMillis;
uint32_t armingMillis;
uint32_t failsafeMillis;
uint32_t endofpathtime = 0;
uint32_t TurnLefttimecomplete = 0; // not used anymore. 
uint32_t brakingtime = 0;
uint32_t adjustingYAWtime = 0;
uint32_t BatteryCompensationtimer;
uint32_t lastvelmillis;
uint32_t turningtime = 0;
uint32_t lastvelmillisl;
uint32_t lastforwardvelmillis;

// Logic Booleans for Naviagtion
bool armingSequenceFlag = false;
volatile bool endofpath = false; // Used to decide when to turn drone
volatile bool turningsoon = false; // used to activate endofpath
volatile bool busychnagingYAW = false;
volatile int turningYAW = 1500;
bool armsequencecomplete = false;
bool runoncePITCH = false;
volatile bool sbusmeesagesent = false;
float BatteryCompensation = 0; // increase by increments of 5. 
bool BatteryCompensationBol = true;
bool armingthrottledone = true;
bool beginpitching = false;

volatile float throttlevelocity = 0;
volatile float olddistance = 0;
bool goingup = false;
bool goingdown = false;

volatile float rollvelocity = 0;
volatile float olddistancel = 0;

volatile float forwardvelocity = 0;
volatile float oldforwarddistance = 0;


boolean start_flag = false;
boolean failsafe_flag = false;

void triggerFailsafe()
{
  Serial.println("Failsafe triggered. Land drone.");
  armingSequenceFlag = false;
  failsafeMillis = millis();
  failsafe_flag = true;
}

/**@brief Function to be executed on Radio Rx Timeout event
 */
void OnRxTimeout(void)
{
  Serial.println("On Rx Timeout CB");
  Serial.printf("OnRxTimeout: No message received in last %d ms \n", RX_TIMEOUT_VALUE);
}

/**@brief Function to be executed on Radio Rx Done event
 */
void OnRxDone(uint8_t *payload, uint16_t size, int16_t rssi, int8_t snr)
{
  if (!start_flag)
  {
    start_flag = true; // For first packet
    armingSequenceFlag = true;
    armingMillis = millis();
  }

  Serial.println("OnRxDone:");

  // Time from last message
  time_t now = millis();
  double time_between_message = (now - lastMessage) / 1000.0;

  Serial.print("Message: ");
  Serial.println((const char *)payload);
  Serial.printf("RssiValue=%d dBm, SnrValue=%d\n", rssi, snr);
  Serial.printf("Time from last message=%.2f seconds \n", time_between_message);

  String payload_str = (const char *)payload;

  if (payload_str == "STOP")
  {
    triggerFailsafe();
  }

  lastMessage = millis();
}

/**@brief Function to be executed on Radio Rx Error event
 */
void OnRxError(void)
{
  Serial.println("OnRxError CB");
}

void setupLoRaModule()
{
  // Define the HW configuration between MCU and SX126x
  hwConfig.CHIP_TYPE = SX1262_CHIP;         // Example uses an eByte E22 module with an SX1262
  hwConfig.PIN_LORA_RESET = PIN_LORA_RESET; // LORA RESET // Note: times out way more often...
  hwConfig.PIN_LORA_NSS = PIN_LORA_NSS;     // LORA SPI CS
  hwConfig.PIN_LORA_SCLK = PIN_LORA_SCLK;   // LORA SPI CLK
  hwConfig.PIN_LORA_MISO = PIN_LORA_MISO;   // LORA SPI MISO
  hwConfig.PIN_LORA_DIO_1 = PIN_LORA_DIO_1; // LORA DIO_1
  hwConfig.PIN_LORA_BUSY = PIN_LORA_BUSY;   // LORA SPI BUSY
  hwConfig.PIN_LORA_MOSI = PIN_LORA_MOSI;   // LORA SPI MOSI
  hwConfig.USE_DIO2_ANT_SWITCH = false;     // Example uses an CircuitRocks Alora RFM1262 which uses DIO2 pins as antenna control
  hwConfig.USE_DIO3_TCXO = false;           // Example uses an CircuitRocks Alora RFM1262 which uses DIO3 to control oscillator voltage
  hwConfig.USE_DIO3_ANT_SWITCH = false;     // Only Insight ISP4520 module uses DIO3 as antenna control
  hwConfig.USE_RXEN_ANT_PWR = false;        // RXEN is used as power for antenna switch

  // Initialize the LoRa chip
  Serial.println("Starting lora_hardware_init");
  uint32_t init_result = 0;

  init_result = lora_hardware_init(hwConfig);
  Serial.printf("LoRa init %s\r\n", init_result == 0 ? "success" : "failed");

  // Initialize the Radio callbacks
  RadioEvents.RxDone = OnRxDone;
  RadioEvents.RxTimeout = OnRxTimeout;
  RadioEvents.RxError = OnRxError;

  // Initialize the Radio
  Radio.Init(&RadioEvents);
  Radio.SetCustomSyncWord(0x1424);

  // Set radio to sleep for next setup
  Radio.Sleep();

  // Set Radio channel
  Radio.SetChannel(RF_FREQUENCY);

  // Set Radio TX configuration
  Radio.SetTxConfig(MODEM_LORA, TX_OUTPUT_POWER, 0, LORA_BANDWIDTH,
                    LORA_SPREADING_FACTOR, LORA_CODINGRATE,
                    LORA_PREAMBLE_LENGTH, LORA_FIX_LENGTH_PAYLOAD_ON,
                    true, 0, 0, LORA_IQ_INVERSION_ON, TX_TIMEOUT_VALUE);

  // Set Radio RX configuration
  Radio.SetRxConfig(MODEM_LORA, LORA_BANDWIDTH, LORA_SPREADING_FACTOR,
                    LORA_CODINGRATE, 0, LORA_PREAMBLE_LENGTH,
                    LORA_SYMBOL_TIMEOUT, LORA_FIX_LENGTH_PAYLOAD_ON,
                    0, true, 0, 0, LORA_IQ_INVERSION_ON, true);

  // Start LoRa
  Serial.println("Starting Radio.Rx");
  Radio.Rx(0);
  // Receiver is non-blocking
  while (!start_flag)
  {
    delay(1000);
    Serial.println("Wait for first packet...");
  }
}

void loraTimerCallback()
{
  time_t currentTime = millis();

  if (currentTime - lastMessage > HOVER_LORA_TIMEOUT)
  {
    Serial.printf("Communications lost to failsafe transceiver for %d ms. \n", currentTime - lastMessage);
    // triggerHoverMode();
    triggerFailsafe();
  }
  else if (currentTime - lastMessage > FAILSAFE_LORA_TIMEOUT)
  {
    Serial.printf("Communications lost to failsafe transceiver for %d ms. \n", currentTime - lastMessage);
    triggerFailsafe();
  }
}

// Ultrasonic Top Interupt Function
void US1_ISR() {
  // Called when pwPin changes
  if (digitalRead(pwPinTop) == HIGH) {
    // Rising edge
    pulseStart1 = micros();
    US_ready1 = false;
  } else {
    // Falling edge
    unsigned long pulseWidthT = micros() - pulseStart1;
    distanceCm1 = pulseWidthT / 57.87;
    US_ready1 = true;
  }
}

// Ultrasonic Front Interupt Function
void USFront_ISR() {
  // Called when pwPin changes
  if (digitalRead(pwPinFront) == HIGH) {
    // Rising edge
    pulseStartF = micros();
    US_readyF = false;
  } else {
    // Falling edge
    unsigned long pulseWidthF = micros() - pulseStartF;
    distanceCmF = pulseWidthF / 57.87;
    US_readyF = true;
  }
}

// Ultrasonic LEFT Interupt Function
void US_LEFT() {
  // Called when pwPin changes
  if (digitalRead(pwPinLeftUS) == HIGH) {
    // Rising edge
    pulseStartL = micros();
    US_readyL = false;
  } else {
    // Falling edge
    unsigned long pulseWidthL = micros() - pulseStartL;
    CurrentDistance_US_L = pulseWidthL / 57.87;
    US_readyL = true;
  }
}

/// Reading RIGHT TOF sensor. 
void readCenterAverage(SparkFun_VL53L5CX &sensor, VL53L5CX_ResultsData &measurementData) {
  if (sensor.isDataReady()) {
    if (sensor.getRangingData(&measurementData)) {
      // total is acutally center average value. 

      int totalSum = 0;
      int totalCount = 0;
      totalAvg = 0;
      int indcenter[] = {5,6,9,10}; // center pixels

      for (int i = 0; i < 4; i++) {
        int index = indcenter[i];
        uint8_t status = measurementData.target_status[index];
        int distance = measurementData.distance_mm[index];
        if (status == 5) { // valid return
          totalSum +=  distance;
          totalCount++;
        }
      }

      if (totalCount > 0) {
        totalAvg = totalSum / totalCount;
        Serial.print("Average total distance (mm): ");
        Serial.println(totalAvg);
      } else {
        totalAvg = -1;
        Serial.println("No valid pixels.");
      }

    } else{
      Serial.println("Failed to get Data!");
    }
  } else{
    // Serial.println("Data was not ready");
  }

}

void setup()
{
  // Initialize Serial for debug output
  Serial.begin(115200);

  delay(1000); // Wait for serial to begin

  Serial.println("=====================================");
  Serial.println("LoRa Drone Receiver");
  Serial.println("=====================================");

  Serial.println(" --- Setup SBUS --- ");

  // Initialise all channels to 1500
  for (uint8_t i = 0; i < SBUS_CHANNEL_NUMBER; i++)
  {
    rcChannels[i] = 1500;
  }
  rcChannels[THROTTLE] = THROTTLE_MIN;

  Serial1.begin(100000, SERIAL_8E2, RX_PIN, TX_PIN, true); // Initialize Serial1 with 100000 baud rate

  // Ultrasonic Interrupt Setup
  pinMode(pwPinTop, INPUT_PULLUP);
  attachInterrupt(digitalPinToInterrupt(pwPinTop), US1_ISR, CHANGE); // USFront_ISR
  attachInterrupt(digitalPinToInterrupt(pwPinFront), USFront_ISR, CHANGE);
  attachInterrupt(digitalPinToInterrupt(pwPinLeftUS),US_LEFT , CHANGE);

  Wire.begin(SDA_PIN, SCL_PIN); // Initialize I2C bus
  Wire.setClock(100000); // Optional: 400 kHz I2C
  delay(50);

  // Initialize TOF Sensor 1
  while (!sensor1.begin()) {
    Serial.println("Sensor 1 not found at 0x29! Retrying...");
    delay(50); // small delay to avoid spamming I2C or Serial
  }
  sensor1.setResolution(4*4);
  imageResolution1 = sensor1.getResolution();
  imageWidth1 = sqrt(imageResolution1);
  Serial.println("Sensor 1 initialized successfully at 0x29");
  delay(50);
  // Start ranging on sensor. 
  Serial.println("Starting ranging on tof sensors...");
  sensor1.setRangingFrequency(60);
  sensor1.startRanging();
  Serial.println("sensor tof is now ranging.");

  // Ultrasonic Begin sensing. 
  pinMode(Ultrasonic_Rx_initialiser, OUTPUT);
  digitalWrite(Ultrasonic_Rx_initialiser, HIGH);
  delay(1);
  digitalWrite(Ultrasonic_Rx_initialiser, LOW);
  delay(1);
  pinMode(Ultrasonic_Rx_initialiser, INPUT);

  delay(100); 
  // Ensure that LoRa is at the END!. 

  setupLoRaModule();
  loraTimer.attach_ms(LORA_TIMER_UDPATE_RATE, loraTimerCallback);
  lastMessage = millis();

  Serial.println(" --- Setup Complete --- ");
}

void loop()
{
  currentMillis = millis();

  if (failsafe_flag) {
    // Reset orientation to 1500
    rcChannels[PITCH] = 1500;
    rcChannels[YAW] = 1500;
    rcChannels[ROLL] = 1500;

    if (currentMillis - failsafeMillis < 3000) {
      rcChannels[THROTTLE] = 1360; // Throttle for 3 secs
    } else {
      rcChannels[AUX3] = 1800; // then kill everything
    }
  }

  // Arming sequence hard coded
  else if (armingSequenceFlag){ // armingSequenceFlag
    // wait 5 seconds then arm
    if (currentMillis > 5000 + armingMillis && currentMillis < 10000 + armingMillis){
      rcChannels[THROTTLE] = THROTTLE_MIN;
      rcChannels[AUX1] = 1800;
      Serial.println("Arm drone.");
    } else if (currentMillis > 10000 + armingMillis && currentMillis < 11000 + armingMillis){ // Wait another 5 seconds before turning on throttle and leave on for 10 seconds
      rcChannels[THROTTLE] = 1380;
      rcChannels[AUX1] = 1800;
      Serial.println("Throttle 1360.");
      BatteryCompensation = 0; // reset battery compensation
      BatteryCompensationBol = true;
    } else if (currentMillis > 11000 + armingMillis){ // 11000 - <11300
      Serial.println("Arming sequence finished");
      rcChannels[THROTTLE] = 1380;
      rcChannels[AUX1] = 1800; 
      armingSequenceFlag = false;
      armsequencecomplete = true;
      armingthrottledone = true;
    }
  }

 //  25/10/2025
 // THe last attempt ended with the drone hitting the ceiling and then riding it. 

  else if(armsequencecomplete){ //armsequencecomplete

        // THROTTLE CHANGES - TOP side Ultrasonic Sensor
    if (US_ready1) {
      // Serial.print("US1 Distance: ");
      CurrentDistance = round(distanceCm1 * 100) / 100;
      Serial.print("Top US:                   ");
      Serial.print(distanceCm1, 2);
      Serial.println(" cm");
      US_ready1 = false;  // Current distance of ultrasonic is saved in: distanceCm1

      // Velocity determination
      throttlevelocity = (CurrentDistance - olddistance) / (millis() - lastvelmillis) * 1000; // cm/s
      lastvelmillis = millis();
      olddistance = CurrentDistance;
      Serial.print("THROTTLE VELOCITY: ");
      Serial.println(throttlevelocity, 2);
      if(throttlevelocity < -5.00){ // falling towards the roof so distance decreases and velocity is negative. 
        goingdown = false;
        goingup = true;
        throttlevelocity = 0.00;
      } else{
        goingdown = true;
        goingup = false;
        throttlevelocity = 0.00;
      }
      // Initial luanch control
      if(armingthrottledone){ // hold throttle until it passes upper limit then commence flight navigation.
        rcChannels[THROTTLE] = 1392; // 1370> ?? <1375
        BatteryCompensation = 0; // reset battery compensation
        if(CurrentDistance < 100.00 ){  
          beginpitching = true; //
          armingthrottledone = false; //
        }
      }
      // Flight Control
      if(!armingthrottledone){
        if(goingup && !goingdown){
          if(CurrentDistance < 50.00){
            rcChannels[THROTTLE] = 1360 + BatteryCompensation; // descend quickly
            // if(BatteryCompensationBol || millis() - BatteryCompensationtimer > 500){
            //   BatteryCompensationBol = false;
            //   BatteryCompensation = BatteryCompensation - 2;
            //   BatteryCompensationtimer = millis();
            // }
          } else if(CurrentDistance > 50.00 && CurrentDistance <  95.00 ){  // 118.23
            rcChannels[THROTTLE] = ((5*CurrentDistance) / 9) + 1332.2 + BatteryCompensation; 
            BatteryCompensationBol = true;
          } else if (CurrentDistance > 95.00 && CurrentDistance <  110.00){ 
            rcChannels[THROTTLE] = 1385 + BatteryCompensation; 
            BatteryCompensationBol = true;
          } else if (CurrentDistance > 110.00 && CurrentDistance <  150.00){  // 122.35
            rcChannels[THROTTLE] = 0.875*CurrentDistance + 1288.75 + BatteryCompensation; 
            BatteryCompensationBol = true;
          } else if(CurrentDistance > 150.00){
            rcChannels[THROTTLE] = 1420 + BatteryCompensation;
            BatteryCompensationBol = true; 
          }
        }
        else if(goingdown && !goingup){
          if(CurrentDistance < 50.00){
            rcChannels[THROTTLE] = 1370 + BatteryCompensation; // descend quickly
          } else if(CurrentDistance > 50.00 && CurrentDistance <  95.00 ){  // 118.23
            rcChannels[THROTTLE] = ((5*CurrentDistance)/9) + 1342.20 + BatteryCompensation; 
            BatteryCompensationBol = true;
          } else if (CurrentDistance > 95.00 && CurrentDistance <  110.00){ 
            rcChannels[THROTTLE] = 1395 + BatteryCompensation; // change to 1395?
            BatteryCompensationBol = true;
          } else if (CurrentDistance > 110.00 && CurrentDistance <  150.00){  // 122.35
            rcChannels[THROTTLE] = 1.125*CurrentDistance + 1271.25 + BatteryCompensation; 
            BatteryCompensationBol = true;
          } else if(CurrentDistance > 150.00){
            rcChannels[THROTTLE] = 1440 + BatteryCompensation; 
            // if(BatteryCompensationBol || millis() - BatteryCompensationtimer > 500){
            //   BatteryCompensationBol = false;
            //   BatteryCompensation = BatteryCompensation + 5;
            //   BatteryCompensationtimer = millis();
            // }
          } 
        }
      }

      if(beginpitching && !endofpath && !turningsoon){
        if(CurrentDistance < 150.00){  
          rcChannels[PITCH] = 1540; // pitch backwards
        } else{  
          rcChannels[PITCH] = 1500; // neutral
        } 
      }
    }


    // // ROLL Changes
    if (US_readyL) {
      // Serial.print("US1 Distance: ");
      Serial.print("LEFT US:      ");
      Serial.print(CurrentDistance_US_L, 2);
      Serial.println(" cm");
      US_readyL = false;  // Current distance of ultrasonic is saved in: distanceCm1

      // Roll Velocity
      rollvelocity = (CurrentDistance_US_L - olddistancel) / (millis() - lastvelmillisl) * 1000; // cm/s
      lastvelmillisl = millis();
      olddistancel = CurrentDistance_US_L;
      Serial.print("ROLL VELOCITY: ");
      Serial.println(rollvelocity, 2);
      // if velocity is negative, drone is flying towards left wall
      // if velocity is positive, drone is flying towards right wall


      if(millis() - turningtime > 360 && !turningsoon){   // currentMillis - TurnLefttimecomplete > 500 
      // Serial.println("IN ROLL if statement");
        if(CurrentDistance_US_L < 65.00 && rollvelocity < 3){ 
          rcChannels[ROLL] = 1525;
        } else if(CurrentDistance_US_L > 65.00 && CurrentDistance_US_L < 75.00 && rollvelocity < 0){ 
            rcChannels[ROLL] = -2.5*CurrentDistance_US_L + 1687.5; // Dampen the turn
        } else if(CurrentDistance_US_L > 75.00 && CurrentDistance_US_L < 85.00 && rollvelocity > 0){ 
            rcChannels[ROLL] = -2.5*CurrentDistance_US_L + 1687.5; // Dampen the turn
        } else if(CurrentDistance_US_L > 85.00 && rollvelocity > -3){ 
          rcChannels[ROLL] = 1475; // left
        } else{  
          rcChannels[ROLL] = 1500;
        }
    } else{
      rcChannels[ROLL] = 1500;
    }
  }

    readCenterAverage(sensor1, measurementData1);

    if (totalAvg > 0){
    forwardvelocity = (totalAvg - oldforwarddistance) / (millis() - lastforwardvelmillis) * 100; // cm/s
    lastforwardvelmillis = millis();
    oldforwarddistance = totalAvg;
    Serial.print("FORWARD VELOCITY: ");
    Serial.println(forwardvelocity, 2);
    }
    // target distance 1000 mm
    // if vel is positivie drone is moving forawrd
    // if vel is negative drone is moving backwards
    // vel should never really be bigger or less than 250 cm/s and -250 cm/s respectively.
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

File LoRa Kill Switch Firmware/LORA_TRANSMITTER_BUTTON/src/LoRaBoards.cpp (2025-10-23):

/**
 * @file      boards.cpp
 * @author    Lewis He (lewishe@outlook.com)
 * @license   MIT
 * @copyright Copyright (c) 2024  ShenZhen XinYuan Electronic Technology Co., Ltd
 * @date      2024-04-24
 * @last-update 2025-05-26
 *
 */

#include "LoRaBoards.h"

#if defined(HAS_SDCARD) && !defined(SD_SHARE_SPI_BUS)
SPIClass SDCardSPI(HSPI);
#endif

#if defined(ARDUINO_ARCH_ESP32)
#if ESP_IDF_VERSION >= ESP_IDF_VERSION_VAL(5,0,0)
#include "hal/gpio_hal.h"
#endif
#include "driver/gpio.h"
#endif //ARDUINO_ARCH_ESP32


DISPLAY_MODEL *u8g2 = NULL;
static DevInfo_t  devInfo;


uint32_t deviceOnline = 0x00;


static void enable_slow_clock();

bool beginDisplay()
{
    Wire.beginTransmission(DISPLAY_ADDR);
    if (Wire.endTransmission() == 0) {
        Serial.printf("Find Display model at 0x%X address\n", DISPLAY_ADDR);
        u8g2 = new DISPLAY_MODEL(U8G2_R2, U8X8_PIN_NONE);
        u8g2->begin();
        u8g2->clearBuffer();
        u8g2->setFont(u8g2_font_inb16_mr);
        u8g2->drawStr(5, 20, "Drone");
        // u8g2->drawHLine(2, 35, 47);
        // u8g2->drawHLine(3, 36, 47);
        // u8g2->drawVLine(45, 32, 12);
        // u8g2->drawVLine(46, 33, 12);
        // u8g2->setFont(u8g2_font_inb16_mf);
        u8g2->drawStr(15, 50, "Failsafe");
        u8g2->sendBuffer();
        u8g2->setFont(u8g2_font_fur11_tf);
        delay(3000);
        return true;
    }

    Serial.printf("Warning: Failed to find Display at 0x%0X address\n", DISPLAY_ADDR);
    return false;
}

#ifdef HAS_SDCARD
bool writeFile(const char *path, const char *buffer)
{
    bool rlst = false;
    File file = SD.open(path, FILE_WRITE);
    if (!file) {
        Serial.println("Failed to open file for writing");
        return false;
    }
    if (file.print(buffer)) {
        Serial.println("File written");
        rlst = true;
    } else {
        Serial.println("Write failed");
        rlst = false;
    }
    file.close();
    return  rlst;
}


bool readFile(const char *path, uint8_t *buffer, size_t size)
{
    File file = SD.open(path, FILE_READ);
    if (!file) {
        Serial.println("Failed to open file for reading");
        return false;
    }
    file.read(buffer, size);
    file.close();
    return false;
}

bool testSDWriteAndRead()
{
    const char *path = "/test_sd.txt";
    const char *message = "This is a string for reading and writing SD card.";
    uint8_t buffer[128] = {0};

    if (!writeFile(path, message)) {
        Serial.println("SD Text write failed");
        return false;
    }
    delay(100);

    readFile(path, buffer, 128);

    if (memcmp(buffer, message, strlen(message)) != 0) {
        Serial.println("SD verification failed");
        return false;
    }
    Serial.println("SD verification successful");
    return true;
}
#endif /*HAS_SDCARD*/

bool beginSDCard()
{
#ifdef HAS_SDCARD
    bool rlst = SD.begin(SDCARD_CS, SDCardSPI);


    if (rlst) {
        uint32_t cardSize = SD.cardSize() / (1024 * 1024);
        Serial.print("Sd Card init succeeded, The current available capacity is ");
        Serial.print(cardSize / 1024.0);
        Serial.println(" GB");
        deviceOnline |= SDCARD_ONLINE;
        return testSDWriteAndRead();
    } else {
        Serial.println("Warning: Failed to init Sd Card");
    }
#endif /*HAS_SDCARD*/
    return false;
}



void printWakeupReason()
{
#ifdef ARDUINO_ARCH_ESP32
    Serial.print("Reset reason:");
    esp_sleep_wakeup_cause_t wakeup_reason;
    wakeup_reason = esp_sleep_get_wakeup_cause();
    switch (wakeup_reason) {
    case ESP_SLEEP_WAKEUP_UNDEFINED:
        Serial.println(" In case of deep sleep, reset was not caused by exit from deep sleep");
        break;
    case ESP_SLEEP_WAKEUP_ALL :
        break;
    case ESP_SLEEP_WAKEUP_EXT0 :
        Serial.println("Wakeup caused by external signal using RTC_IO");
        break;
    case ESP_SLEEP_WAKEUP_EXT1 :
        Serial.println("Wakeup caused by external signal using RTC_CNTL");
        break;
    case ESP_SLEEP_WAKEUP_TIMER :
        Serial.println("Wakeup caused by timer");
        break;
    case ESP_SLEEP_WAKEUP_TOUCHPAD :
        Serial.println("Wakeup caused by touchpad");
        break;
    case ESP_SLEEP_WAKEUP_ULP :
        Serial.println("Wakeup caused by ULP program");
        break;
    default :
        Serial.printf("Wakeup was not caused by deep sleep: %d\n", wakeup_reason);
        break;
    }
#endif
}
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

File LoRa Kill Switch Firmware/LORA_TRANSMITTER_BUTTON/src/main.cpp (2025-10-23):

// Adapted from RadioLib Transmit with Interrupts Example from RadioLib Library
// https://github.com/Xinyuan-LilyGO/LilyGo-LoRa-Series/tree/master/examples/RadioLibExamples/Transmit_Interrupt


#include "LoRaBoards.h"
#include <RadioLib.h>

#define CONFIG_RADIO_FREQ           915.0
#define CONFIG_RADIO_OUTPUT_POWER   22
#define CONFIG_RADIO_BW             125.0

#define BOOT_BUTTON 0
#define RED_BUTTON 42

// Define radio object
SX1262 radio = new Module(RADIO_CS_PIN, RADIO_DIO1_PIN, RADIO_RST_PIN, RADIO_BUSY_PIN);

void drawMain(); // Function declaration
void drawInstructions();


// save transmission state between loops
static int transmissionState = RADIOLIB_ERR_NONE;
// flag to indicate that a packet was sent
static volatile bool transmittedFlag = false;
static volatile bool failsafeFlag = false;
static uint32_t counter = 0;
static String payload;

// this function is called when a complete packet
// is transmitted by the module
// IMPORTANT: this function MUST be 'void' type
//            and MUST NOT have any arguments!
void setFlag(void)
{
    // we sent a packet, set the flag
    transmittedFlag = true;
}

void interruptCallback() {

    // if failsafe button was pressed, set the flag
    failsafeFlag = true;
}

void setup()
{
    setupBoards();

    // When the power is turned on, a delay is required.
    delay(1500);

    // initialize radio with default settings
    int state = radio.begin();

    printResult(state == RADIOLIB_ERR_NONE);

    Serial.printf("[%s]:", RADIO_TYPE_STR);
    Serial.print(F("Radio Initializing ... "));
    if (state == RADIOLIB_ERR_NONE) {
        Serial.println(F("success!"));
    } else {
        Serial.print(F("failed, code "));
        Serial.println(state);
        while (true);
    }

    // set the function that will be called
    // when packet transmission is finished
    radio.setPacketSentAction(setFlag);

    /*
    *   Sets carrier frequency.
    *   SX1268/SX1262 : Allowed values are in range from 150.0 to 960.0 MHz.
    * * * */
    if (radio.setFrequency(CONFIG_RADIO_FREQ) == RADIOLIB_ERR_INVALID_FREQUENCY) {
        Serial.println(F("Selected frequency is invalid for this module!"));
        while (true);
    }

    /*
    *   Sets LoRa link bandwidth.
    *   SX1268/SX1262 : Allowed values are 7.8, 10.4, 15.6, 20.8, 31.25, 41.7, 62.5, 125.0, 250.0 and 500.0 kHz.
    * * * */
    if (radio.setBandwidth(CONFIG_RADIO_BW) == RADIOLIB_ERR_INVALID_BANDWIDTH) {
        Serial.println(F("Selected bandwidth is invalid for this module!"));
        while (true);
    }


    /*
    * Sets LoRa link spreading factor.
    * SX1262        :  Allowed values range from 5 to 12.
    * * * */
    if (radio.setSpreadingFactor(7) == RADIOLIB_ERR_INVALID_SPREADING_FACTOR) {
        Serial.println(F("Selected spreading factor is invalid for this module!"));
        while (true);
    }

    /*
    * Sets LoRa coding rate denominator.
    * SX1278/SX1276/SX1268/SX1262 : Allowed values range from 5 to 8. Only available in LoRa mode.
    * * * */
    if (radio.setCodingRate(7) == RADIOLIB_ERR_INVALID_CODING_RATE) {
        Serial.println(F("Selected coding rate is invalid for this module!"));
        while (true);
    }

    /*
    * Sets transmission output power.
    * SX1262        :  Allowed values are in range from -9 to 22 dBm. This method is virtual to allow override from the SX1261 class.
    * * * */
    if (radio.setOutputPower(CONFIG_RADIO_OUTPUT_POWER) == RADIOLIB_ERR_INVALID_OUTPUT_POWER) {
        Serial.println(F("Selected output power is invalid for this module!"));
        while (true);
    }

    /*
    * Sets current limit for over current protection at transmitter amplifier.
    * SX1262/SX1268 : Allowed values range from 45 to 120 mA in 2.5 mA steps and 120 to 240 mA in 10 mA steps.
    * NOTE: set value to 0 to disable overcurrent protection
    * * * */
    if (radio.setCurrentLimit(140) == RADIOLIB_ERR_INVALID_CURRENT_LIMIT) {
        Serial.println(F("Selected current limit is invalid for this module!"));
        while (true);
    }

    /*
    * Sets preamble length for LoRa or FSK modem.
    * SX1262/SX1268 : Allowed values range from 1 to 65535.
    * * */
    if (radio.setPreambleLength(16) == RADIOLIB_ERR_INVALID_PREAMBLE_LENGTH) {
        Serial.println(F("Selected preamble length is invalid for this module!"));
        while (true);
    }

    /*
    * Sets LoRa sync word.
    * SX1278/SX1276/SX1268/SX1262/SX1280 : Sets LoRa sync word. Only available in LoRa mode.
    * * */
    if (radio.setSyncWord(0x1424) != RADIOLIB_ERR_NONE) {
        Serial.println(F("Unable to set sync word!"));
        while (true);
    }

    // Enables or disables CRC check of received packets.
    if (radio.setCRC(false) == RADIOLIB_ERR_INVALID_CRC_CONFIGURATION) {
        Serial.println(F("Selected CRC is invalid for this module!"));
        while (true);
    }


    // Setup up failsafe button
    pinMode(RED_BUTTON, INPUT); // Pulled down on PCB

    // Print instructions to screen
    drawInstructions();

    // Wait for start button to be pressed
    while(!digitalRead(RED_BUTTON)) {
    }
    delay(1000); // Delay for debounce

    attachInterrupt(digitalPinToInterrupt(RED_BUTTON), interruptCallback, RISING);

    // start transmitting the first packet
    Serial.print(F("Radio Sending first packet ... "));

    // you can transmit C-string or Arduino string up to
    // 256 characters long
    transmissionState = radio.startTransmit("#0");

}

void loop()
{
    // check if the previous transmission finished
    if (transmittedFlag) {

        // reset flag
        transmittedFlag = false;

        flashLed();
        
        if (transmissionState == RADIOLIB_ERR_NONE) {
            // packet was successfully sent
            Serial.println(F("transmission finished!"));
            // NOTE: when using interrupt-driven transmit method,
            //       it is not possible to automatically measure
            //       transmission data rate using getDataRate()
        } else {
            Serial.print(F("failed, code "));
            Serial.println(transmissionState);
        }


        drawMain();
        // wait a second before transmitting again
        delay(1000);

        // send another one
        Serial.print(F("Radio Sending another packet ... "));

        // you can transmit C-string or Arduino string up to
        // 256 characters long

        if (failsafeFlag) {
            payload = "STOP";
        } else {
            payload = "#" + String(counter++);
        }
        transmissionState = radio.startTransmit(payload);
    }
}
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

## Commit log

2025-07-24 Initial format for sensor data.
2025-07-24 Creation of sensor test data with 10 lines.
2025-08-29 added github repo
    [T-Beam-Shiled-V1.0.dxf, T3S3 V1.3.dxf, T3_V1.3.dwg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]
2025-08-30 Pingpong code now working on ESP32 Dev Module
2025-09-04 esp32-s3 now works
2025-09-08 fixed lora dev kit code
    [main.cpp]
2025-09-12 added reset back in to improve robustness
    [main.cpp]
2025-09-12 currently cleaning up code for failsafe button
    [main.cpp]
2025-09-23 updated screen and button
2025-09-25 update button to match pcb
2025-10-10 fixed settings for single wire antenna
    [LoRa_SX1262.h, main.cpp]
2025-10-22 fixed lora for drone pcb
    [LoRa_SX1262.h, main.cpp]
2025-10-23 completed LoRa kill switch README.md
2025-10-27 updated lora test code to have less print statements
2025-10-27 added PCB files
    [3V3BEC.kicad_sch, 5VBEC.kicad_sch, ABM8AIG-8.000MHZ-1Z-T.step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]
2025-10-27 added CAD files
    [3V3BEC.kicad_sch, 5VBEC.kicad_sch, ABM8AIG-8.000MHZ-1Z-T.step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]
2025-10-27 Delete CAD Design/Full Model
    oops
2025-10-27 Add files via upload
    Full Model
    [Drone_3D_Model.f3d]
2025-10-27 Fixed header file error
    [main.cpp]
2025-10-28 added STL files
    [LAUNCHPAD.stl, LAUNCHRAIL.stl]
2025-10-28 added sensor mount STL files
    [SENSOR_MOUNT_1.stl, SENSOR_MOUNT_2.stl, SENSOR_MOUNT_3.stl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]
2025-10-28 fixed folder structure
    [Ultra_MB1030.csv, data_times.csv, download_imu_cropped.csv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]
